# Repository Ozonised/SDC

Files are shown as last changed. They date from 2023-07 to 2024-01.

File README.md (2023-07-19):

# SDC
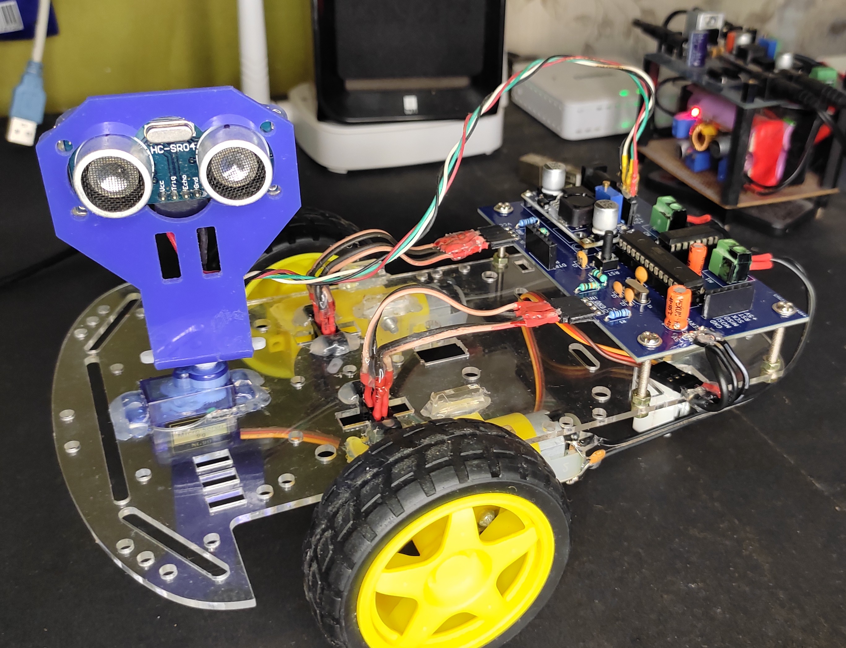
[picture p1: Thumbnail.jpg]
Thumbnail

ATmega 8 based self driving car.

Watch the [YouTube](https://studio.youtube.com/video/CVWcEM45d_U/edit) video to develop some comprehension.

# SETTING UP ATMEGA 8
The ATmega 8 is programmed using an ICSP programmer. In my case, I used an Arduino UNO as an ICSP programmer.
By default, the microcontroller uses the internal 8MHz internal PC oscillator, but we want to use an external 16 MHz oscillator.
So we need to make certain changes to the fuse bits of the ATmega 8. Below are the steps to do so:
1. Download and install AVRDude. AVRDude is the program used by Arduino IDE and PlatformIO to upload your code to an AVR microcontroller.
2. Open up the Arduino IDE, select ```ArduinoISP``` under File/Examples/ and hit upload.
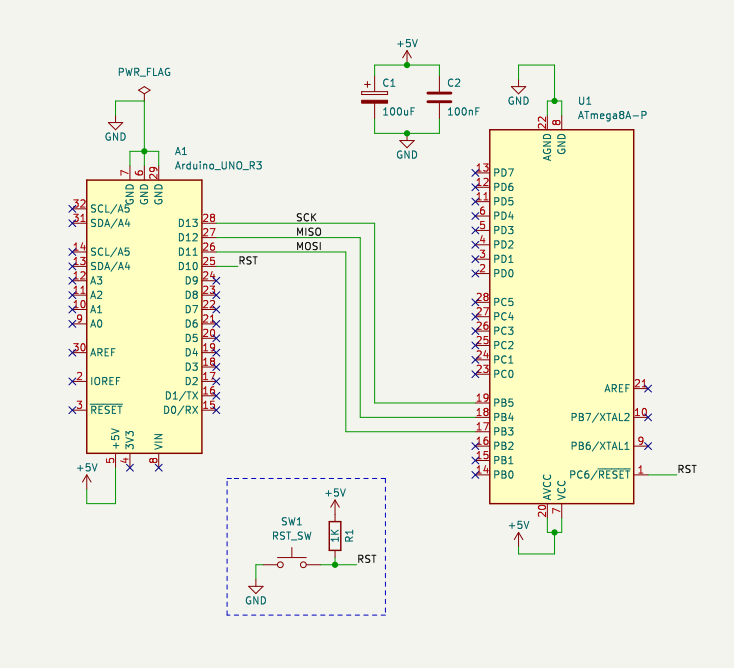
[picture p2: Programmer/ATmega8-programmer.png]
ATmega8 programmer
3. Wire up the Arduino and ATmega8 as shown in the [schematic](/Programmer/ATmega8-programmer.pdf): 
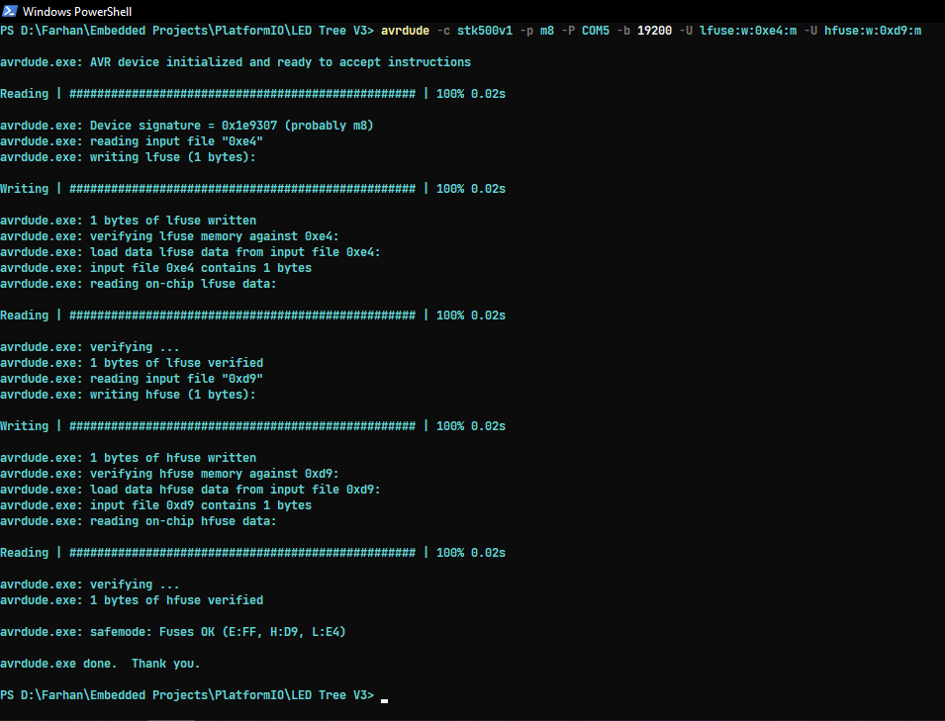
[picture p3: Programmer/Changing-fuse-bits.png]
Changing lfuse
4. By default, the low fuse of the ATmega8 is set to 0xE1. This must be set to 0xE4 to configure the microcontroller to run at 8MHz. Type ``` avrdude -c stk500v1  -P COM5 -p atmega8 -b 19200 -U lfuse:w:0xe4:m -U hfuse:w:0xd9:m ```. Alternatively, you can use an online [AVR fuse bit calculator](https://www.engbedded.com/fusecalc/) for your selected microcontroller. 
### Note: 
The ```-P <port>```argument specifies the connection port. In my case, the arduino is connected to ```COM5``` and hence the argument ```-P COM5```. For ```-p <partno>``` either ```-p m8``` or ```-p atmega8``` can be used. Refer this [guide](https://www.ladyada.net/learn/avr/avrdude.html) for more information.

5. That is all. The ATmega8 is now ready to be programmed with PlatformIO using the arduino as an ISP programmer.

# PART LIST:
You can find the component list [here](SDC_Schematic/SDC_Schematic.csv).

The case along with the motor is available here: https://quartzcomponents.com/products/2wd-smart-robot-car-chassis-kit

MOC7811 optical encoders: https://quartzcomponents.com/products/moc-7811-encoder-sensor

Servo: https://quartzcomponents.com/products/tower-pro-sg90-servo-9-gms-mini-micro-servo-motor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

HCSR04(Ultrasonic sensor): https://quartzcomponents.com/products/hc-sr04-ultrasonic-sensor-module?_pos=1&_sid=1f37cc7e0&_ss=r

Ultrasonic sensor mount: https://quartzcomponents.com/products/ultrasonic-sensor-mounting-bracket-for-hc-sr04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

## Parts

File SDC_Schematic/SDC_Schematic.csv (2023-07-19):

Date: | Wed 19 Jul 2023 08:33:07 PM IST
Component Count: | 27
Item | Qty | Reference(s) | Value | LibPart | Footprint | Datasheet | DNP
1 | 2 | C1, C2 | 22pF | Device:C_Small | Capacitor_THT:C_Disc_D3.0mm_W2.0mm_P2.50mm | ~
2 | 3 | C3, C4, C5 | 100nF | Device:C_Small | Capacitor_THT:C_Disc_D5.0mm_W2.5mm_P2.50mm | ~
3 | 1 | C6 | 100uF | Device:C_Polarized | Capacitor_THT:CP_Radial_D6.3mm_P2.50mm | ~
4 | 1 | C7 | 220uF | Device:C_Polarized | Capacitor_THT:CP_Radial_D6.3mm_P2.50mm | ~
5 | 2 | J1, J2 | Screw_Terminal_01x02 | Connector:Screw_Terminal_01x02 | TerminalBlock:TerminalBlock_Altech_AK300-2_P5.00mm | ~
6 | 3 | J4, J5, J8 | Conn_01x04 | Connector_Generic:Conn_01x04 | Connector_PinSocket_2.54mm:PinSocket_1x04_P2.54mm_Vertical | ~
7 | 2 | J6, J9 | Conn_01x06_Socket | Connector:Conn_01x06_Socket | Connector_PinSocket_2.54mm:PinSocket_1x06_P2.54mm_Horizontal | ~
8 | 1 | J7 | Conn_01x03_Pin | Connector:Conn_01x03_Pin | Connector_PinHeader_2.54mm:PinHeader_1x03_P2.54mm_Vertical | ~
9 | 1 | J10 | Jack-DC | Connector:Jack-DC | Connector_BarrelJack:BarrelJack_Horizontal | ~
10 | 3 | R1, R4, R5 | 10K | Device:R | Resistor_THT:R_Axial_DIN0207_L6.3mm_D2.5mm_P7.62mm_Horizontal | ~
11 | 3 | R2, R3, R6 | 680 | Device:R | Resistor_THT:R_Axial_DIN0207_L6.3mm_D2.5mm_P7.62mm_Horizontal | ~
12 | 1 | SW1 | SW_SPST | Switch:SW_SPST | Button_Switch_THT:SW_PUSH_6mm_H4.3mm | ~
13 | 1 | U1 | ATmega8A-P | MCU_Microchip_ATmega:ATmega8A-P | Package_DIP:DIP-28_W7.62mm | http://ww1.microchip.com/downloads/en/DeviceDoc/Microchip%208bit%20mcu%20AVR%20ATmega8A%20data%20sheet%2040001974A.pdf
14 | 1 | U2 | L293D | Driver_Motor:L293D | Package_DIP:DIP-16_W7.62mm | http://www.ti.com/lit/ds/symlink/l293.pdf
15 | 1 | U4 | LM2596_module | lm2596_module:LM2596_module | lm2596_module:LM2596_module
16 | 1 | Y1 | 16MHz | Device:Crystal_Small | Crystal:Crystal_HC49-4H_Vertical | ~

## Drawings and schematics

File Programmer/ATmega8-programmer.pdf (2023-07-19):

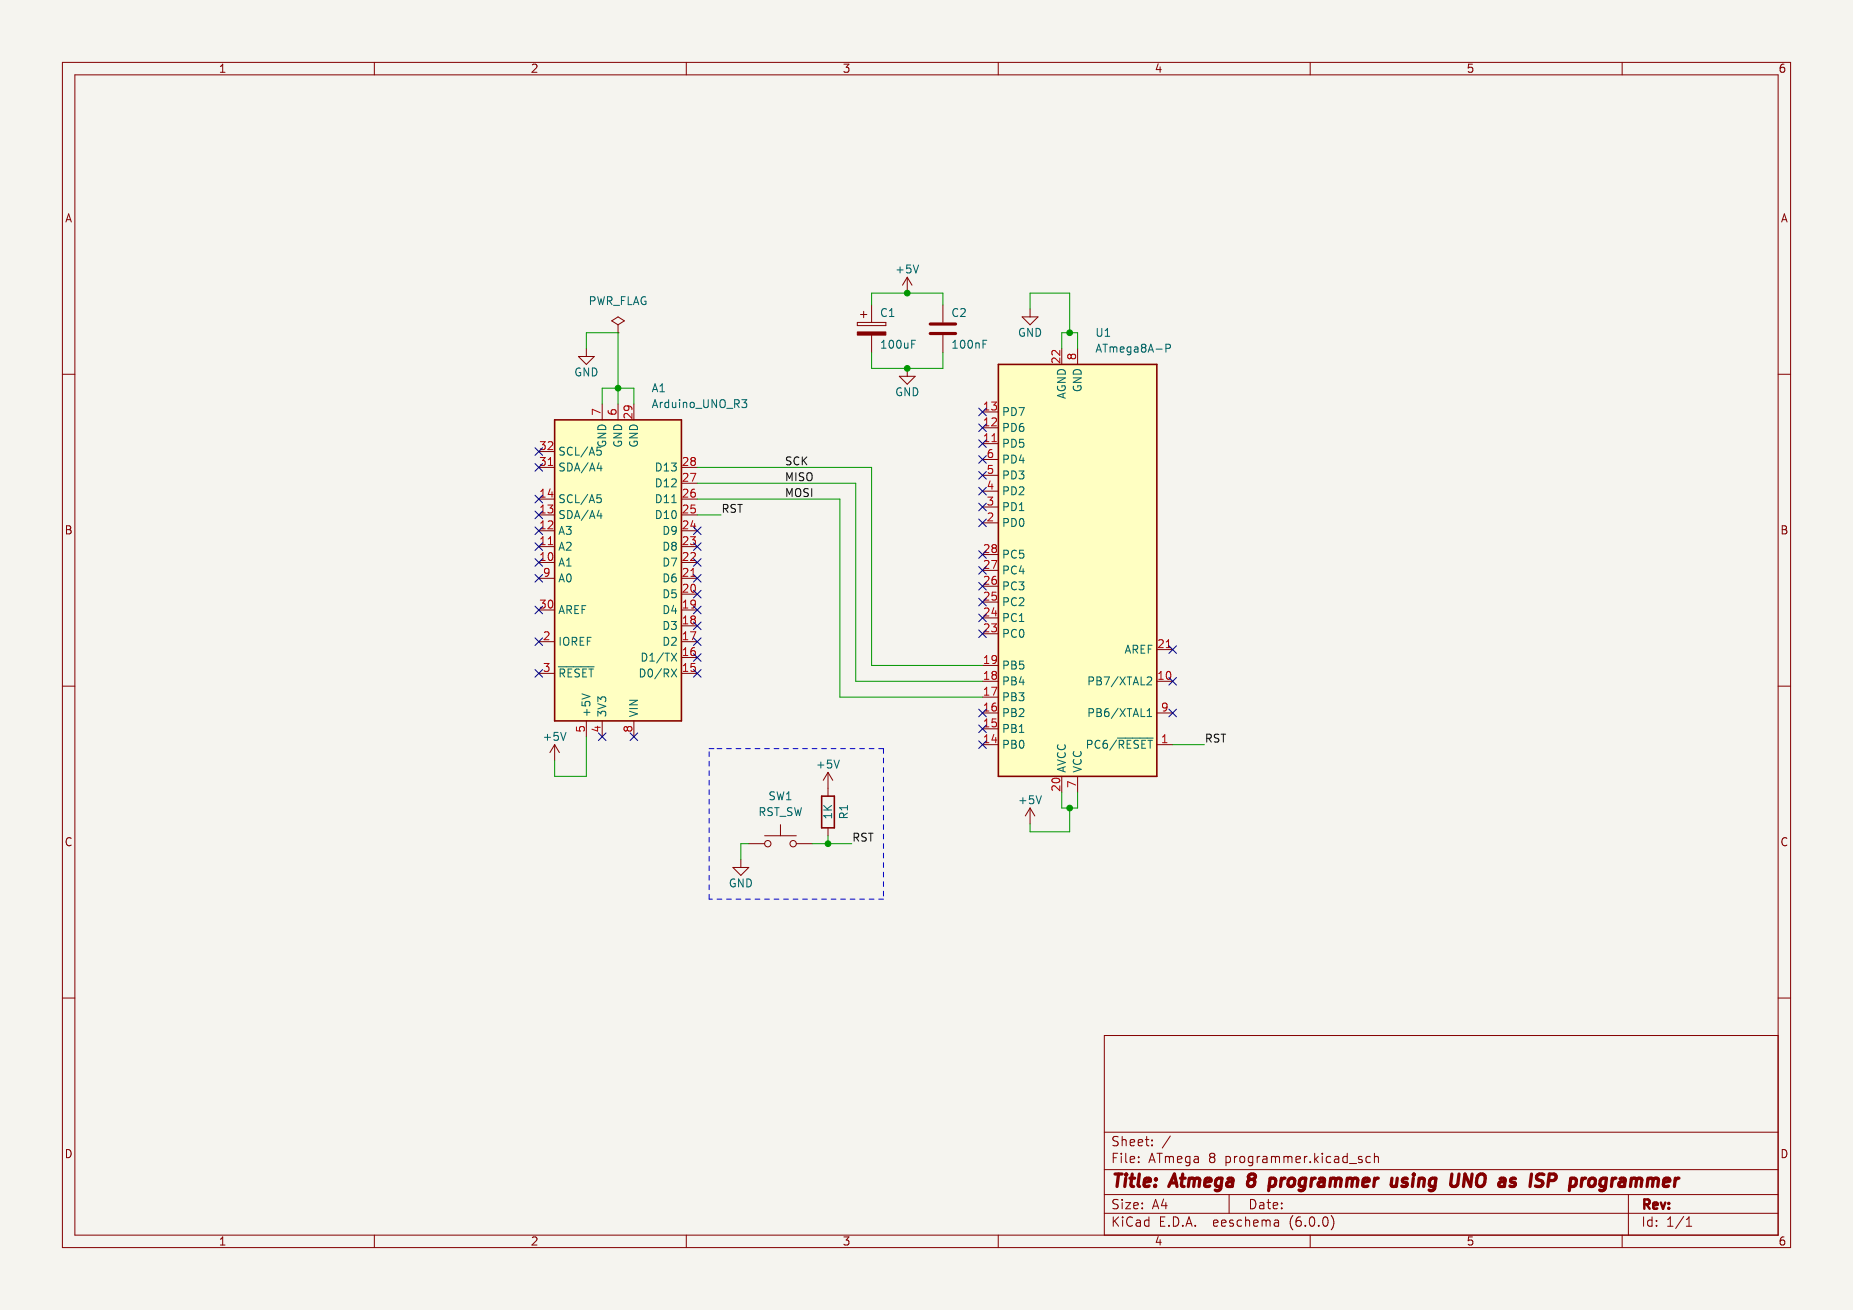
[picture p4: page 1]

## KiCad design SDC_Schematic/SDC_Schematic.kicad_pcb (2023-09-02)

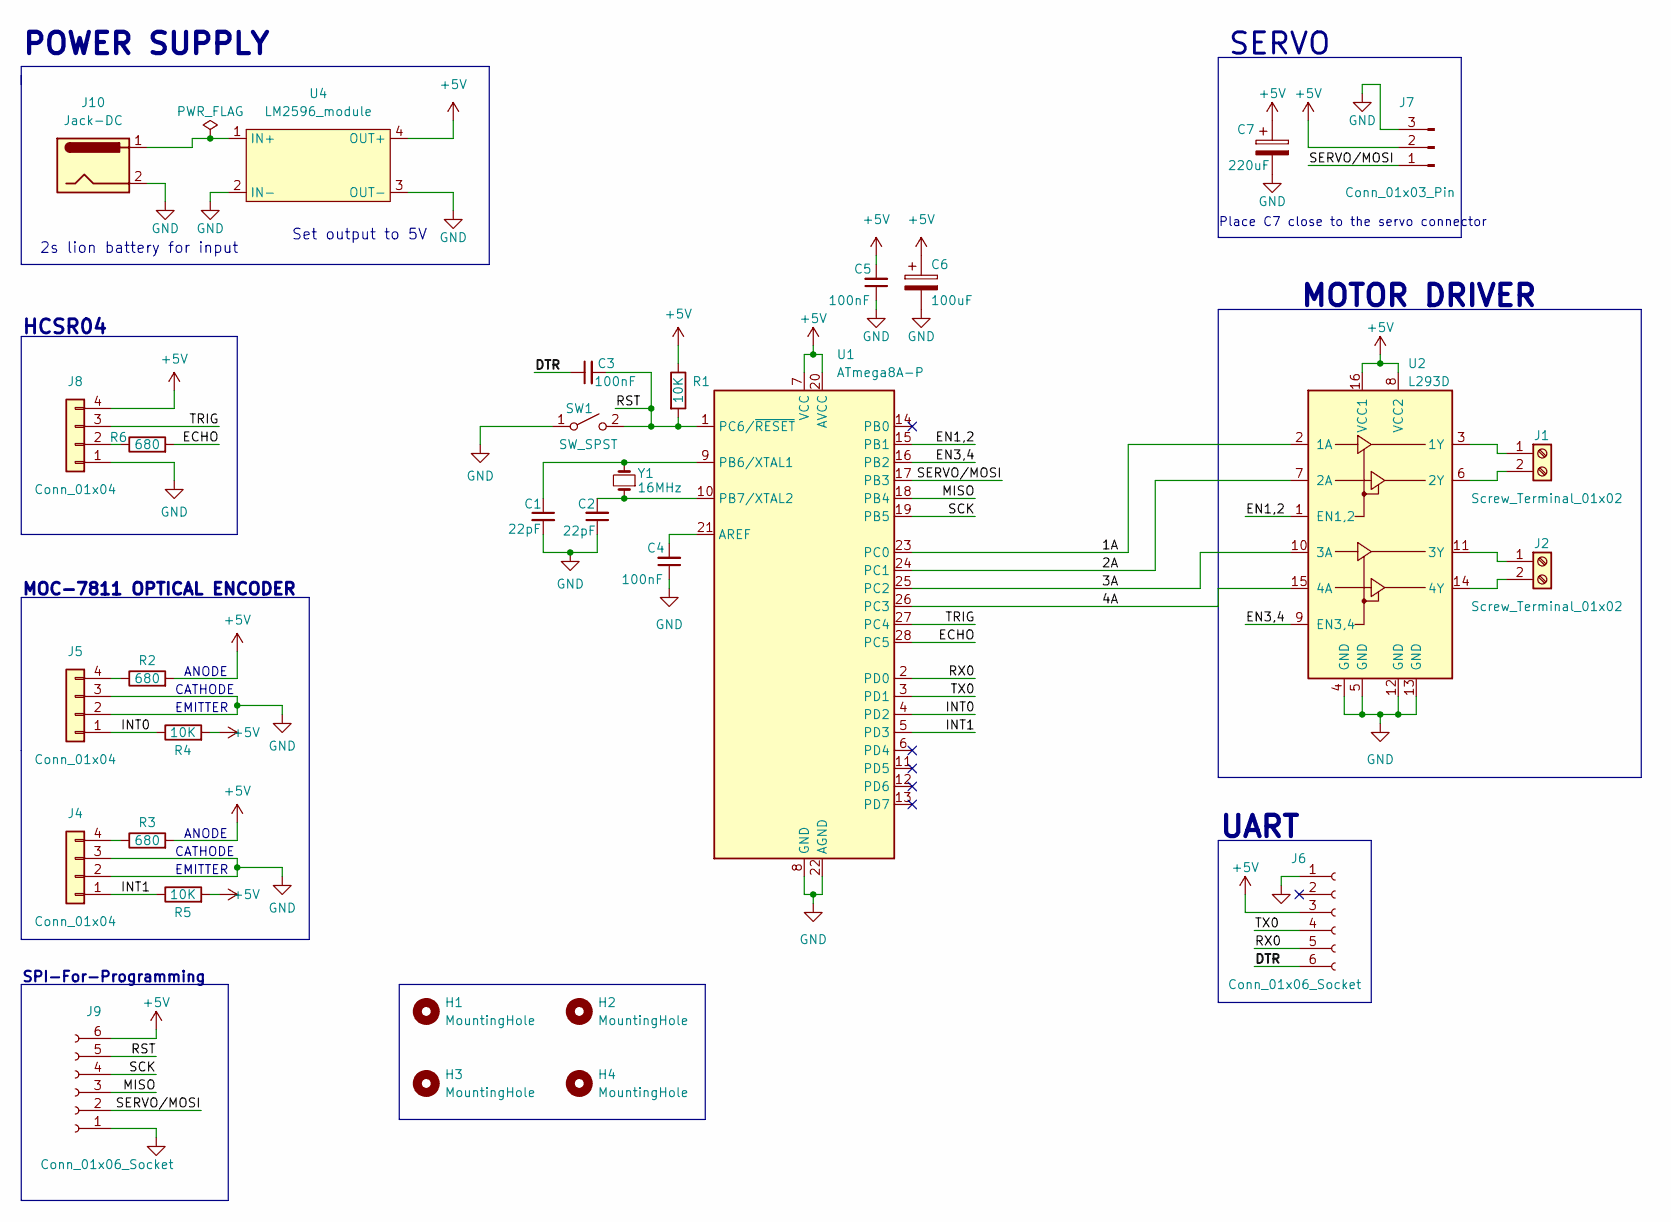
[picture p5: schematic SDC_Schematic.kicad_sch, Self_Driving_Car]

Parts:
C1, C2: 22pF; C_Disc_D3.0mm_W2.0mm_P2.50mm
C3, C4, C5: 100nF; C_Disc_D5.0mm_W2.5mm_P2.50mm
C6: 100uF; CP_Radial_D6.3mm_P2.50mm
C7: 220uF; CP_Radial_D6.3mm_P2.50mm
H1, H2, H3, H4: MountingHole; MountingHole_3.5mm
J1, J2: Screw_Terminal_01x02; TerminalBlock_Altech_AK300-2_P5.00mm
J4, J5, J8: Conn_01x04; PinSocket_1x04_P2.54mm_Vertical
J6, J9: Conn_01x06_Socket; PinSocket_1x06_P2.54mm_Vertical
J7: Conn_01x03_Pin; PinHeader_1x03_P2.54mm_Vertical
J10: Jack-DC; BarrelJack_Horizontal
R1, R4, R5: 10K; R_Axial_DIN0207_L6.3mm_D2.5mm_P7.62mm_Horizontal
R2, R3, R6: 680; R_Axial_DIN0207_L6.3mm_D2.5mm_P7.62mm_Horizontal
SW1: SW_SPST; SW_PUSH_6mm_H4.3mm
U1: ATmega8A-P; DIP-28_W7.62mm
U2: L293D; DIP-16_W7.62mm
U4: LM2596_module
Y1: 16MHz; Crystal_HC49-4H_Vertical

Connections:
+5V: C5.2, C6.1, C7.1, J6.3, J7.2, J8.4, J9.6, R1.1, R2.2, R3.2, R4.2, R5.2, U1.7 (VCC), U1.20 (AVCC), U2.8 (VCC2), U2.16 (VCC1), U4.4 (OUT+)
/1A: U1.23 (PC0), U2.2 (1A)
/2A: U1.24 (PC1), U2.7 (2A)
/3A: U1.25 (PC2), U2.10 (3A)
/4A: U1.26 (PC3), U2.15 (4A)
/DTR: C3.1, J6.6
/ECHO: R6.2, U1.28 (PC5)
/EN1,2: U1.15 (PB1), U2.1 (EN1,2)
/EN3,4: U1.16 (PB2), U2.9 (EN3,4)
/INT0: J5.1, R4.1, U1.4 (PD2)
/INT1: J4.1, R5.1, U1.5 (PD3)
/MISO: J9.3, U1.18 (PB4)
/RST: C3.2, J9.5, R1.2, SW1.2 (B), U1.1 (PC6/~RESET)
/RX0: J6.5, U1.2 (PD0)
/SCK: J9.4, U1.19 (PB5)
/SERVO/MOSI: J7.1, J9.2, U1.17 (PB3)
/TRIG: J8.3, U1.27 (PC4)
/TX0: J6.4, U1.3 (PD1)
GND: C1.2, C2.1, C4.1, C5.1, C6.2, C7.2, J4.2, J4.3, J5.2, J5.3, J6.1, J7.3, J8.1, J9.1, J10.2, SW1.1 (A), U1.8 (GND), U1.22 (AGND), U2.4 (GND), U2.5 (GND), U2.12 (GND), U2.13 (GND), U4.2 (IN-), U4.3 (OUT-)
unnamed: J1.1, U2.3 (1Y)
unnamed: J1.2, U2.6 (2Y)
unnamed: J2.1, U2.11 (3Y)
unnamed: J2.2, U2.14 (4Y)
unnamed: J4.4, R3.1
unnamed: J5.4, R2.1
unnamed: J8.2, R6.1
unnamed: C4.2, U1.21 (AREF)
unnamed: C1.1, U1.9 (PB6/XTAL1), Y1.2
unnamed: C2.2, U1.10 (PB7/XTAL2), Y1.1
unnamed: J10.1, U4.1 (IN+)

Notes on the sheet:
HCSR04
Set output to 5V
SPI-For-Programming
MOTOR DRIVER
2s lion battery for input
EMITTER
ANODE
SERVO
Place C7 close to the servo connector
CATHODE
POWER SUPPLY
MOC-7811 OPTICAL ENCODER
UART

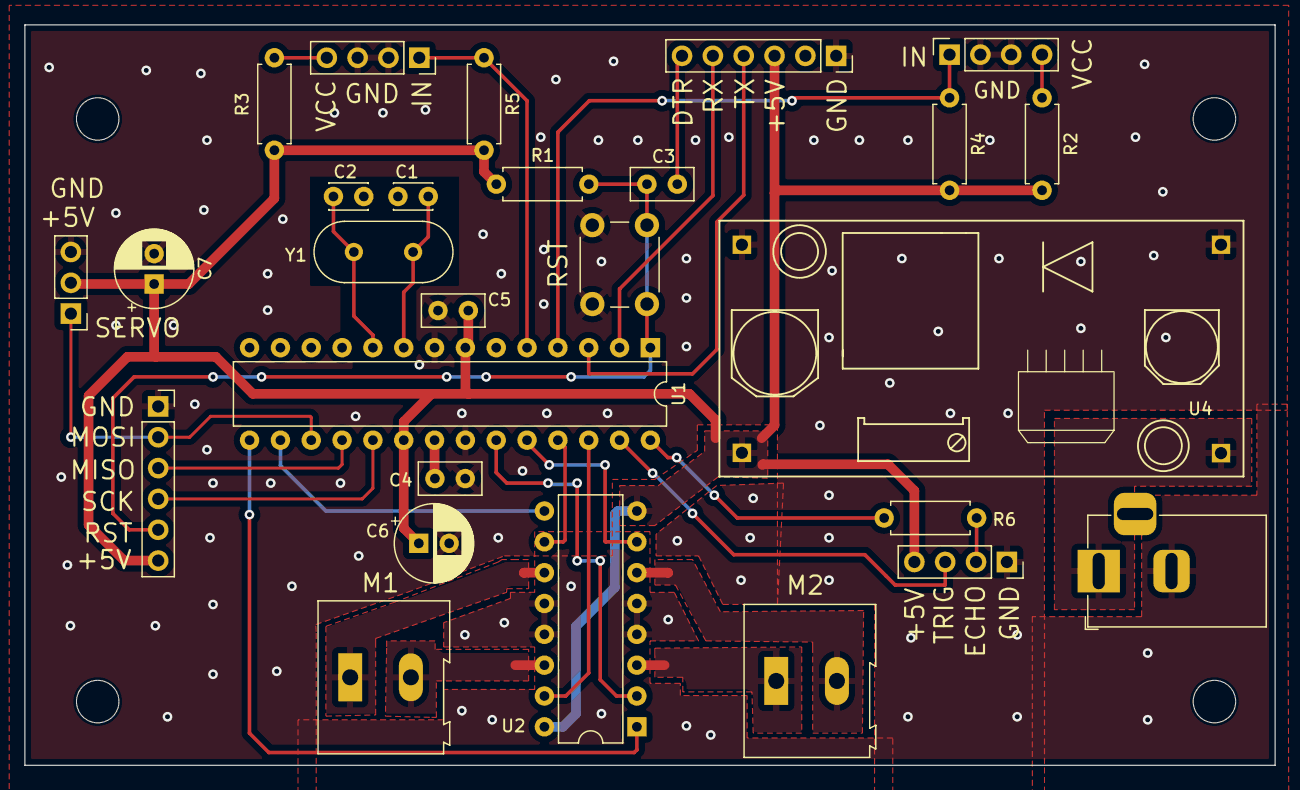
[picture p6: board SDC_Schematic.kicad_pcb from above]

Board: 2 copper layers, 103.0 x 61.0 mm, 31 parts (0 on the bottom side), 30 nets.

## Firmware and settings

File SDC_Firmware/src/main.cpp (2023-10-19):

#include <Arduino.h>

#include "hcsr04.h"
#include "state.h"

// HCSR04 pins
const uint8_t TRIG_PIN = A4, ECHO_PIN = A5;

HCSR04 hcsr04(TRIG_PIN, ECHO_PIN);

void (*currentState)(void);

void setup(void)
{
  PID_Init();
  Motor::Init();
  Servo::Init();
  currentState = scanArea;
  // the first reading on start up from the hcsr04 can be erroneous, so we just run it once to ignore the first reading
  hcsr04.getDistance();
  hcsr04.distance = 0;
}

void loop(void)
{
  currentState();
}

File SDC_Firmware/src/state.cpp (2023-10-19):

#include "state.h"

static const uint8_t maintainDistance = 20; // distance to be maintained between the object and vechicle
// static const uint8_t encoderSlotsCount = 20;       // no of slots on the encoder wheel
// static const float wheelCircumference = 19;

static const uint8_t motorTicksToTurn = 10; // no of ticks to make a 90 degree turn

static unsigned long currentMillis, prevMillis;
static const unsigned long loopPeriod = 60; // loop period in ms

PID drivePID(255, -255, 0.06);
PID turnPID(255, -255, 0.06);

void PID_Init()
{
    drivePID.setPoint = maintainDistance;
    drivePID.KP = -23;
    turnPID.KD = 0.28;
    turnPID.setPoint = motorTicksToTurn;
    turnPID.KP = 25;
    turnPID.KD = 0.15;
}

void scanArea()
{
    static uint8_t servoAngles[3] = {0, 90, 180};
    uint8_t maxDistanceServoAngle; // The  servo angle at which the measured distance is maximum
    unsigned short objectDistance = 0;

    Servo::Set(90);
    delay(200);

    objectDistance = hcsr04.getDistance();

    if (objectDistance > maintainDistance)
    {
        dir = Direction::FORWARD;
    }
    else
    {
        // scan the space in a 180 degree arc and find the servo angle at which there's maximum distance available
        for (uint8_t i = 0; i < 3; i++)
        {
            Servo::Set(servoAngles[i]);
            delay(200);
            if (hcsr04.getDistance() > objectDistance)
            {
                objectDistance = hcsr04.distance;
                maxDistanceServoAngle = servoAngles[i];
            }
        }

        if (maxDistanceServoAngle < 90)
            dir = Direction::RIGHT;
        else if (maxDistanceServoAngle > 90)
            dir = Direction::LEFT;
        else
            dir = Direction::FORWARD;
    }

    currentState = drive;
}

void drive()
{
    unsigned long temp_left_motor_count = 0, temp_right_motor_count = 0, average_motor_count = 0, prev_motor_count = 0;
    unsigned short measurement;
    short pwm;

    Servo::Set(90);
    delay(200);

    while (dir == Direction::LEFT || dir == Direction::RIGHT)
    {
        currentMillis = millis();

        if ((currentMillis - prevMillis) > loopPeriod)
        {
            cli();
            temp_right_motor_count = Motor::Right::count;
            temp_left_motor_count = Motor::Left::count;
            sei();

            average_motor_count = (temp_left_motor_count + temp_right_motor_count) / 2;
            pwm = turnPID.calculate(average_motor_count);

            Motor::Move(dir, pwm, pwm);

            if (turnPID.error <= -1)
            {
                Motor::Move(Direction::STOP);
                dir = Direction::FORWARD;
                cli();
                Motor::Left::count = 0;
                Motor::Right::count = 0;
                sei();
            }

            prevMillis = currentMillis;
        }
    }

    while (dir == Direction::FORWARD || dir == Direction::BACK)
    {
        currentMillis = millis();

        if (currentMillis - prevMillis >= loopPeriod)
        {
            measurement = hcsr04.getDistance();

            cli();
            temp_right_motor_count = Motor::Right::count;
            temp_left_motor_count = Motor::Left::count;
            sei();

            average_motor_count = (temp_left_motor_count + temp_right_motor_count) / 2;

            pwm = drivePID.calculate(measurement);

            if (drivePID.error < 0)
                dir = Direction::FORWARD;
            else if (drivePID.error > 0)
                dir = Direction::BACK;

            if (pwm < 0)
                pwm *= -1;

            Motor::Move(dir, pwm, pwm);

            // if the vechicle is off by 2cm from the maintainDistance
            // prev_motor_count == average_motor_count ,i.e, the vechicle is not moving
            if (drivePID.error <= 2 && drivePID.error >= -2 && prev_motor_count == average_motor_count)
            {
                dir = Direction::STOP;
                Motor::Move(dir);
            }

            prevMillis = currentMillis;
            prev_motor_count = average_motor_count;
        }
    }
    currentState = scanArea;
}

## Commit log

2023-07-19 Programer
    added schematic for programming the ATmega 8
2023-07-19 modified schematic
    added SPI port, capacitors for the servo & uC and barrel jack for power input
    [SDC_Schematic.kicad_sch]
2023-07-19 added part list
    [SDC_Schematic.csv, SDC_Schematic.kicad_sch]
2023-07-20 added mounting hole
    [SDC_Schematic.kicad_sch]
2023-09-02 Schematic and PCB
    updated schematic symbols and connections as well as created a PCB along with gerber files
    [SDC_Schematic-B_Cu.gbl, SDC_Schematic-B_Mask.gbs, SDC_Schematic-B_Paste.gbp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]
2023-09-02 L293d driver
    made correction to left and right direction control
2023-10-06 modified PCB and schematic
2023-10-06 updated schematic and PCB
    [SDC_Schematic-B_Cu.gbl, SDC_Schematic-B_Mask.gbs, SDC_Schematic-B_Paste.gbp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]
2023-10-06 added PID lib
2023-10-14 modified servoSet
    fixed issue where the servo wouldn't turn 180 and 0 completely
2023-10-15 modified servo and l293d lib
    placed servo's and motor's init and move function in their respective namespaces
2023-10-19 added motor count for each motor
2023-10-19 modified drive scanArea & added PID_init
    added pid control for driving forward and making turns
    Condensed scanArea()
2024-01-22 updated thumbnail
    [SDC_Schematic-B_Cu.gbl, SDC_Schematic-B_Mask.gbs, SDC_Schematic-B_Paste.gbp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]
